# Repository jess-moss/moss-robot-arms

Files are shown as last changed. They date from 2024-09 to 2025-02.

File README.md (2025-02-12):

> [!IMPORTANT]
> For use with [LeRobot](https://github.com/huggingface/lerobot)  we now recommend building or purchasing the [SO100](https://github.com/TheRobotStudio/SO-ARM100) arm instead. While the Moss v1 robot is still supported, it will be deprecated. Additionally, 3D-printed parts for the SO100 are now available for purchase if you don't have a printer. If you already have a Moss v1, you could disassemble it and create a SO100 using the same motors. 
>
> For instructions on building and setting up the SO100, follow this [tutorial](https://github.com/huggingface/lerobot/blob/main/examples/10_use_so100.md).

# moss-robot-arms
moss-robot-arms Beta version 1.0.

A repository for affordable, easy-to-assemble robot arms designed for teleoperation applications. 

## Assembly Instructions

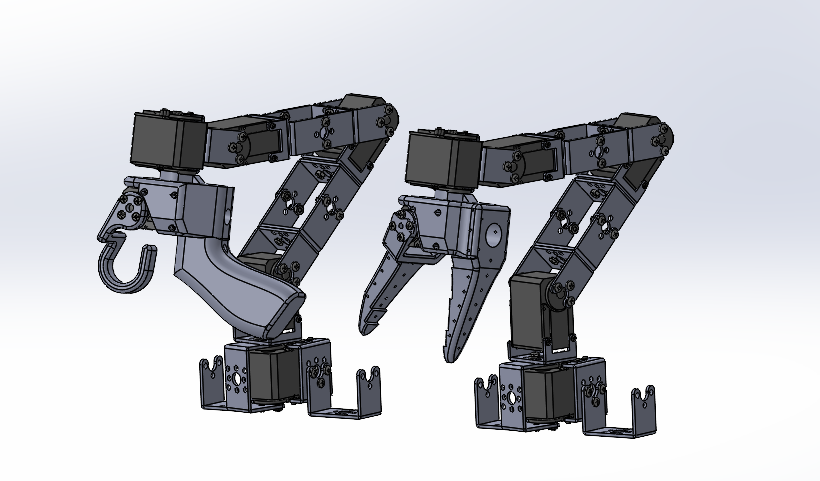
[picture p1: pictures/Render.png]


## Sourcing Parts
Note: The follower and leader arm for this teleoperation setup will have the same off the shelf parts. If you plan on creating the classic teleoperation set up to be used with the `LeRobot` library please buy from the Parts for 2 arms below. Note prices and items may vary slightly depending on geographic location.

/!\ Warning: We only have links for US, EU and CN for now. If you find links for other countries, please create an issue or PR so that we add them to the list.

### Parts For Two Arms (Standard Teleoperation Setup):
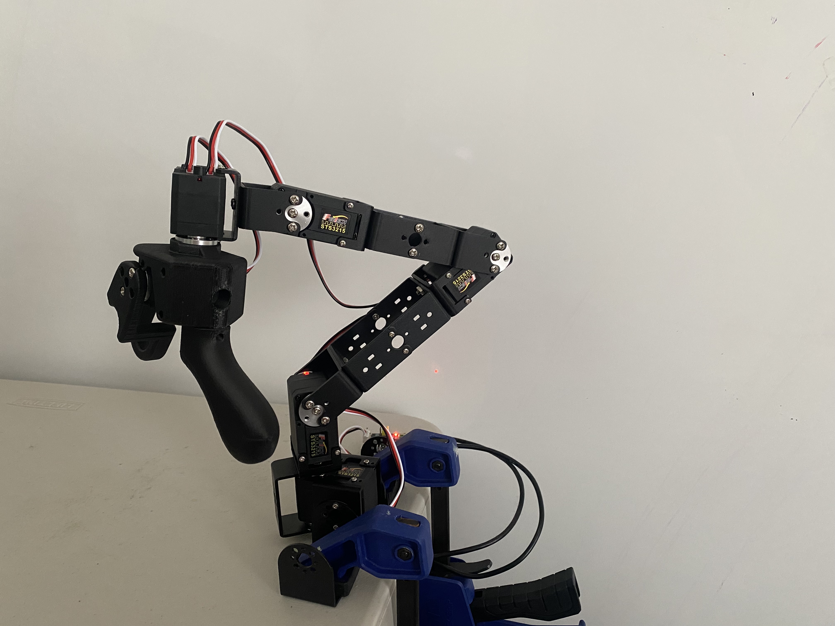
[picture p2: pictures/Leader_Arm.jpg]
Leader Arm
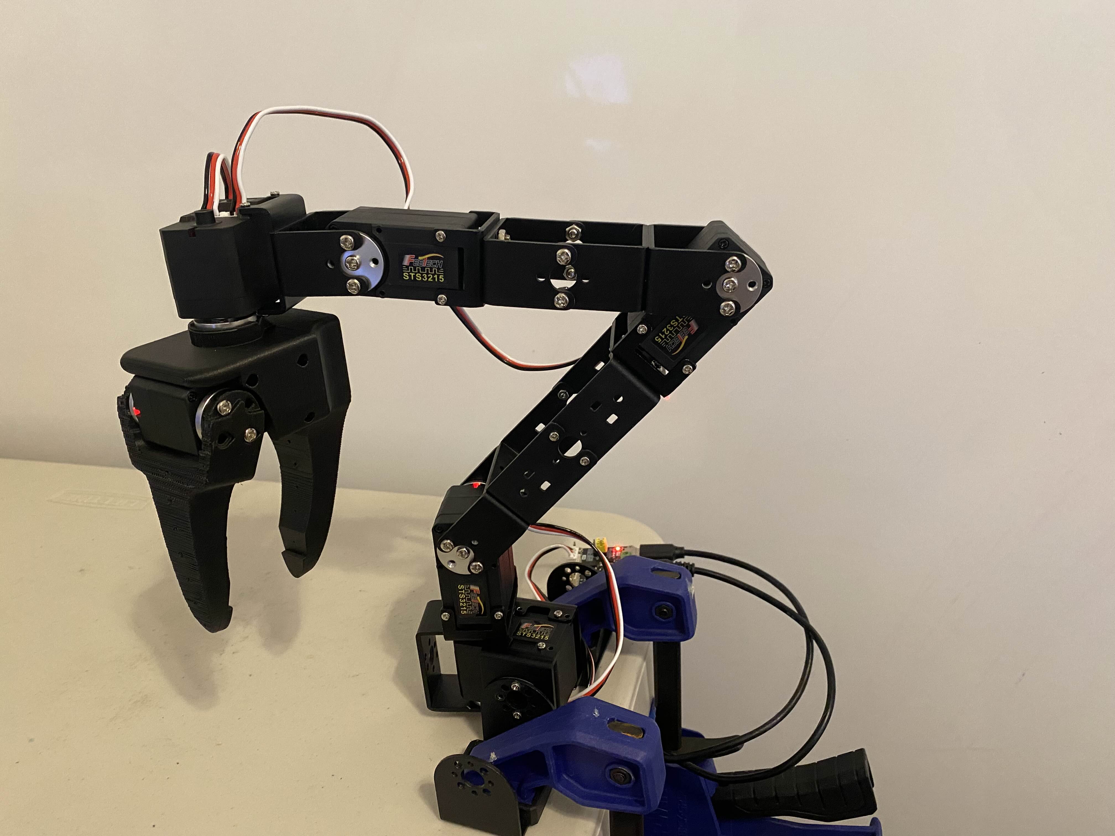
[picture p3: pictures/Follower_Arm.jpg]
Follower Arm
 

| Part | Amount | Unit Cost (US) | Buy US | Unit Cost (EU) | Buy EU | Unit Cost (RMB) | Buy CN |
|---|---|---|---|---|---|---|---|
| STS3215 Servo<sup>[1](#myfootnote1)</sup> | 12 | $14 | [Alibaba](https://www.alibaba.com/product-detail/Top-Seller-Low-Cost-Feetech-STS3215_1600999461525.html) | 13€ | [Alibaba](https://www.alibaba.com/product-detail/Top-Seller-Low-Cost-Feetech-STS3215_1600999461525.html) | ￥97.72 | [TaoBao](https://item.taobao.com/item.htm?id=712179366565&skuId=5268252241438) |
| Motor Control Board | 2 | $5 | [Waveshare](https://www.waveshare.com/bus-servo-adapter-a.htm) - [Amazon](https://www.amazon.com/Control-Circuit-Suitable-Supports-Controlling/dp/B0CKT8BN73/ref=asc_df_B0CKT8BN73/) | 4€ | [Waveshare](https://www.waveshare.com/bus-servo-adapter-a.htm)-[Amazon](https://www.amazon.fr/-/en/dp/B0CJ6RYC9J/ref=sr_1_3)| ￥27 | [TaoBao](https://detail.tmall.com/item.htm?id=738817173460&skuId=5096283384143) |
| Bracket Set | 20 | $3 | [Alibaba](https://www.alibaba.com/product-detail/STS3215-Metal-brackets-for-FEETECH-7_1600836829515.html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) | 2€ | [Alibaba](https://www.alibaba.com/product-detail/STS3215-Metal-brackets-for-FEETECH-7_1600836829515.html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) | --- | --- |
| U Bracket | 20 | --- | --- | --- | --- | ￥6 | [TaoBao](https://item.taobao.com/item.htm?id=615340872015&skuId=4472922777845) |
| Bottom Bracket | 6 | --- | --- | --- | --- | ￥6 | [TaoBao](https://item.taobao.com/item.htm?id=615340872015&skuId=4472922777847) |
| Side Bracket | 6 | --- | --- | --- | --- | ￥6 | [TaoBao](https://item.taobao.com/item.htm?id=615340872015&skuId=4472922777846) |
| USB-C Cable 2 pcs | 1 | $7 | [Amazon](https://www.amazon.com/Charging-etguuds-Charger-Braided-Compatible/dp/B0B8NWLLW2/?th=1) | 7€ | [Amazon](https://www.amazon.fr/dp/B07BNF842T) | ￥23.9*2 | [TaoBao](https://detail.tmall.com/item.htm?id=44425281296&skuId=5611379016222) |
| Power Supply<sup>[2](#myfootnote2)</sup> | 2 | $10 | [Amazon](https://www.amazon.com/Facmogu-Switching-Transformer-Compatible-5-5x2-1mm/dp/B087LY41PV/) | 13€ | [Amazon](https://www.amazon.fr/-/en/dp/B01HRR9GY4/) | ￥22.31 | [TaoBao](https://item.taobao.com/item.htm?id=544824248494&skuId=4974994129990) |
| Table Clamp 4pcs | 1 | $9 | [Amazon](https://www.amazon.com/dp/B0CY899V9V) | 8€ | [Amazon](https://www.amazon.fr/-/en/dp/B08HZ1QRBF/)| ￥7.8 | [TaoBao](https://detail.tmall.com/item.htm?id=738636473238&skuId=5505939904942) |
| Lowstrength Threadlocker<sup>[3](#myfootnote3)</sup> | 1 | $9 | [Amazon](https://www.amazon.com/Loctite-Threadlocker-Automotive-High-Temperature-Non-Corrosive/dp/B0002KKTT0/)| 11€ | [Amazon](https://www.amazon.fr/-/en/dp/B000HBGHFY/) | ￥81 | [TaoBao](https://detail.tmall.com/item.htm?id=652665229827&skuId=5125512809535) |
| Screwdriver Set (includes Phillips #000, #00, #0, #1) | 1 | $6 | [Amazon](https://www.amazon.com/Precision-Phillips-Screwdriver-Electronics-Computer/dp/B0DB227RTH) | 10€ | [Amazon](https://www.amazon.fr/dp/B08ZXVMVYD/) | ￥14.9 | [TaoBao](https://detail.tmall.com/item.htm?id=675684600845&skuId=4856851392176) |
| Wrench<sup>[4](#myfootnote5)</sup> | 1 | $5 | [Amazon](https://www.amazon.com/uxcell-Metric-Double-Wrench-5-5mm/dp/B07D4B8GWW/) | 4€ | [Amazon](https://www.amazon.fr/-/en/dp/B075DML8KB/) | ￥8.9 | [TaoBao](https://detail.tmall.com/item.htm?id=735857252241&skuId=5685349146062) |
| Total |---| $288 |---| 274€ |---|￥1631.46|---|

### Parts for One Arm:

| Part | Amount | Unit Cost (US) | Buy US | Unit Cost (EU) | Buy EU | Unit Cost (RMB) | Buy CN |
|---|---|---|---|---|---|---|---|
| STS3215 Servo<sup>[1](#myfootnote1)</sup> | 6 | $14 | [Alibaba](https://www.alibaba.com/product-detail/Top-Seller-Low-Cost-Feetech-STS3215_1600999461525.html) | 13€ | [Alibaba](https://www.alibaba.com/product-detail/Top-Seller-Low-Cost-Feetech-STS3215_1600999461525.html) | ￥97.72 | [TaoBao](https://item.taobao.com/item.htm?id=712179366565&skuId=5268252241438) |
| Motor Control Board | 1 | $5 | [Waveshare](https://www.waveshare.com/bus-servo-adapter-a.htm) - [Amazon](https://www.amazon.com/Control-Circuit-Suitable-Supports-Controlling/dp/B0CKT8BN73/ref=asc_df_B0CKT8BN73/) | 4€ | [Waveshare](https://www.waveshare.com/bus-servo-adapter-a.htm)-[Amazon](https://www.amazon.fr/-/en/dp/B0CJ6RYC9J/ref=sr_1_3)| ￥27 | [TaoBao](https://detail.tmall.com/item.htm?id=738817173460&skuId=5096283384143) |
| Bracket Set | 10 | $3 | [Alibaba](https://www.alibaba.com/product-detail/STS3215-Metal-brackets-for-FEETECH-7_1600836829515.html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) | 2€ | [Alibaba](https://www.alibaba.com/product-detail/STS3215-Metal-brackets-for-FEETECH-7_1600836829515.html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) | --- | --- |
| U Bracket | 10 | --- | --- | --- | --- | ￥6 | [TaoBao](https://item.taobao.com/item.htm?id=615340872015&skuId=4472922777845) |
| Bottom Bracket | 3 | --- | --- | --- | --- | ￥6 | [TaoBao](https://item.taobao.com/item.htm?id=615340872015&skuId=4472922777847) |
| Side Bracket | 3 | --- | --- | --- | --- | ￥6 | [TaoBao](https://item.taobao.com/item.htm?id=615340872015&skuId=4472922777846) |
| USB-C Cable 2 pcs | 1 | $7 | [Amazon](https://www.amazon.com/Charging-etguuds-Charger-Braided-Compatible/dp/B0B8NWLLW2/?th=1) | 7€ | [Amazon](https://[www.amazon.com/Charging-etguuds-Charger-Braided-Compatible/dp/B0B8NWLLW2/?th=1](https://www.amazon.fr/dp/B07BNF842T/)) | ￥23.9 | [TaoBao](https://detail.tmall.com/item.htm?id=44425281296&skuId=5611379016222) |
| Power Supply<sup>[2](#myfootnote2)</sup> | 1 | $10 | [Amazon](https://www.amazon.com/Facmogu-Switching-Transformer-Compatible-5-5x2-1mm/dp/B087LY41PV/) | 13€ | [Amazon](https://www.amazon.fr/-/en/dp/B01HRR9GY4/) | ￥22.31 | [TaoBao](https://item.taobao.com/item.htm?id=544824248494&skuId=4974994129990) |
| Table Clamp 2pcs | 1 | $5 | [Amazon](https://www.amazon.com/Clamp-Hanger-Storage-Clamps-Mount/dp/B0C1GYSVCS?rps=1&sr=1-2) | 8€ | [Amazon](https://www.amazon.fr/-/en/dp/B08HZ1QRBF/)| ￥7.8 | [TaoBao](https://detail.tmall.com/item.htm?id=738636473238&skuId=5505939904942) |
| Lowstrength Threadlocker<sup>[3](#myfootnote3)</sup> | 1 | $9 | [Amazon](https://www.amazon.com/Loctite-Threadlocker-Automotive-High-Temperature-Non-Corrosive/dp/B0002KKTT0/)| 11€ | [Amazon](https://www.amazon.fr/-/en/dp/B000HBGHFY/) | ￥81 | [TaoBao](https://detail.tmall.com/item.htm?id=652665229827&skuId=5125512809535) |
| Screwdriver Set (includes Phillips #000, #00, #0, #1) | 1 | $6 | [Amazon](https://www.amazon.com/Precision-Phillips-Screwdriver-Electronics-Computer/dp/B0DB227RTH) | 10€ | [Amazon](https://www.amazon.fr/dp/B08ZXVMVYD/) | ￥14.9 | [TaoBao](https://detail.tmall.com/item.htm?id=675684600845&skuId=4856851392176) |
| Wrench<sup>[4](#myfootnote4)</sup> | 1 | $5 | [Amazon](https://www.amazon.com/uxcell-Metric-Double-Wrench-5-5mm/dp/B07D4B8GWW/) | 4€ | [Amazon](https://www.amazon.fr/-/en/dp/B075DML8KB/) | ￥8.9 | [TaoBao](https://detail.tmall.com/item.htm?id=735857252241&skuId=5685349146062) |
| Total |---| $159 |---| 153€ |---|868.13|---|

## Printing the Parts
A variety of 3D printers are acceptable to print the parts necessary of the follower and leader arm. Follow the steps below to ensure a good print.

1. Choose a printer: The STL files provided ready to print on many FDM printers. Below are the tested and suggested settings though others may work.
   1. Material: PLA
   2. Nozzle Diameter and Precision: 0.4mm nozzle diameter at 0.2mm layer height or 0.6mm nozzle at 0.4mm layer height.
   3. Infill Density: 13%
   4. Sample Printers: [Prusa Mini+](https://www.prusa3d.com/product/original-prusa-mini-semi-assembled-3d-printer-4/), [UP Plus 2](https://shop.tiertime.com/product/tiertime-up-plus-2-3d-printer/), [Ender3](https://www.amazon.com/Comgrow-Creality-Ender-Aluminum-220x220x250mm/dp/B07BR3F9N6/).
2. Set up the printer
   1. Setup and Takedown
      1. Ensure that the printer is calibrated and the bed level is correctly set using the printer specific instructions.
      2. Clean the print bed, making sure it is free from dust, or grease. If cleaning the bed using water, or other liquid, dry the bed.
      3. If your printer recommends it, use a standard glue stick and apply a thin, even layer of glue across the print area of the bed. Avoid clumping or uneven application.
      4. Load the printer filament using printer specific instructions.
      5. Ensure the printer settings match the ones suggested above (most printers have multiple settings so choose the ones that most closely match).
      6. Set for supports everywhere but ignore slopes greater than 45 degrees to the horizontal.
      7. There should be no supports in the screw holes with horizontal axes.
3. Print the two files found in `so_100_gripper_parts`, which are listed below.
   1. `Print_Follower_SO_ARM100_08k_Gripper.STL`
   2. `Print_Leader_SO_ARM100_08k_Gripper.STL`
4. Take Down
   1. After the print is done, use the putty knife to scrape the parts off the print bed.
   2. Remove any support material from parts.
   3. Reapply the glue stick before starting the next print.

## Assembling the Parts
Construct the leader and follower arms using the [Assembly Video](https://www.youtube.com/watch?v=DA91NJOtMic). After you assemble the two arms from the video, power the leader and follower arm using the 5V power supplies. In addition, plug each arm into your computer using a USB-C cable.

## Configure
While this robot can be programmed in a variety of manners, it is suggested to use with [LeRobot](https://github.com/huggingface/lerobot/blob/main/examples/7_get_started_with_real_robot.md).

Join the project for support and development on the [discord server](https://discord.gg/ggrqhPTsMe).

## Footnotes
<a name="myfootnote1">1</a>: The STS3215 arm comes in two sizes. The 7.4V has a stall torque of 16.5kg.cm at 6V (and likely slightly less for a 5V power supply). The 12V version has a stall torque of 30kg.cm. While we found the 7.4V to be sufficient, if you would like more powerful motors you can buy the 12V version [here](https://www.alibaba.com/product-detail/12V-30KG-STS3215-High-Torque-Intelligent_1600990786556.html). Note if you do this, you will also have to buy a 12V 5A+ power supply instead of a 5V one above, but all other components will remain the same.\
<a name="myfootnote2">2</a>: IMPORTANT: If you buy the 12V STS3215 motors, you should buy the [12V 5A+ power supply](https://www.amazon.com/Converter-100-220V-Transformer-5-5x2-1mm-Accessories/dp/B08C594VNP/) instead of the 5V power supply provided. \
<a name="myfootnote3">3</a>: While Loctite is not strictly necessary, it does help to ensure screws do not loosen overtime, and is recommended whenever you have a the M3 screw fastening into the M3 nut. You only need a small dot of it. \
<a name="myfootnote4">4</a>: You can either use a 5.5mm or 7/32" wrench, as they are both compatible with the M3 nuts. In a pinch you can also use needle-nose or other pliers but a wrench does help with assembly.

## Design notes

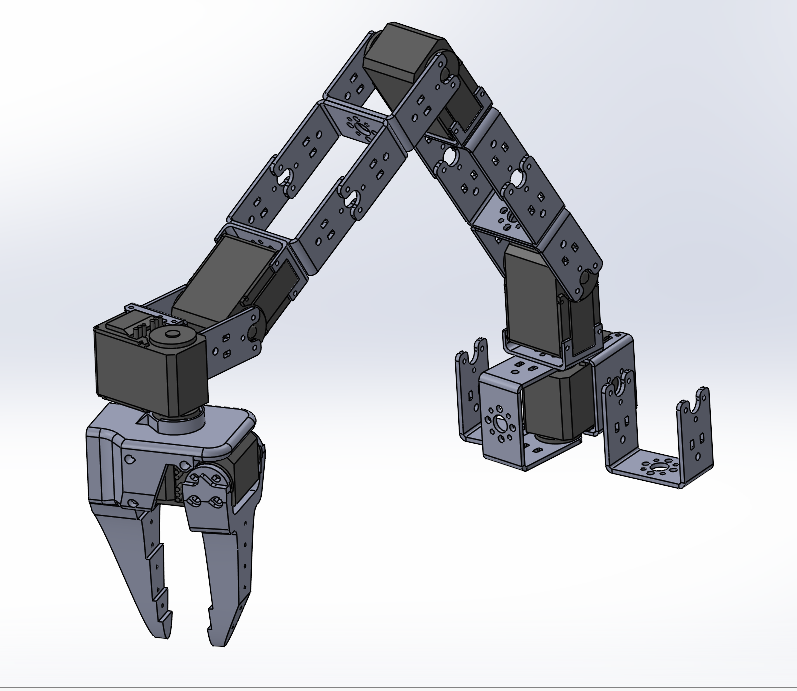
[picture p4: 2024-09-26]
pictures/Follower_Render.png

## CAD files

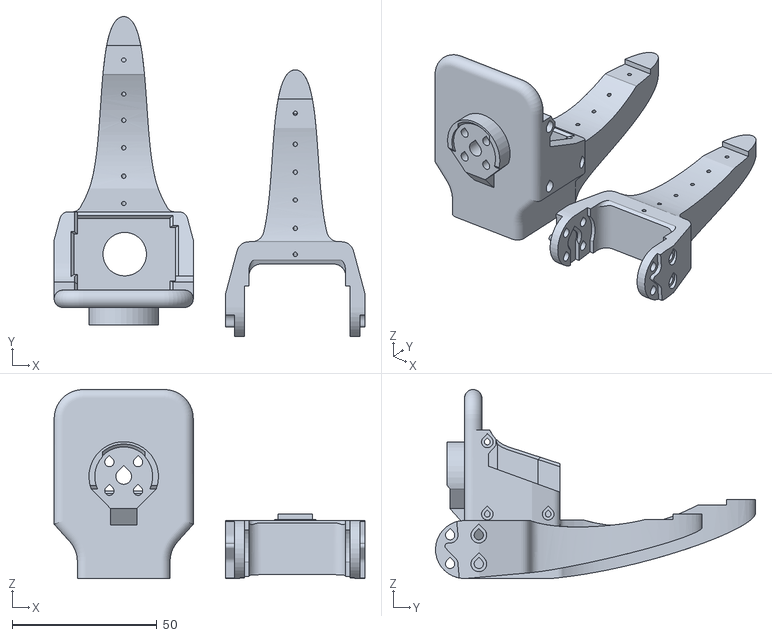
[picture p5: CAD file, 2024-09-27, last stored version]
so_100_gripper_parts/follower_gripper/SO_100_Follower_Gripper.STL
107.2 x 110.4 x 65.2

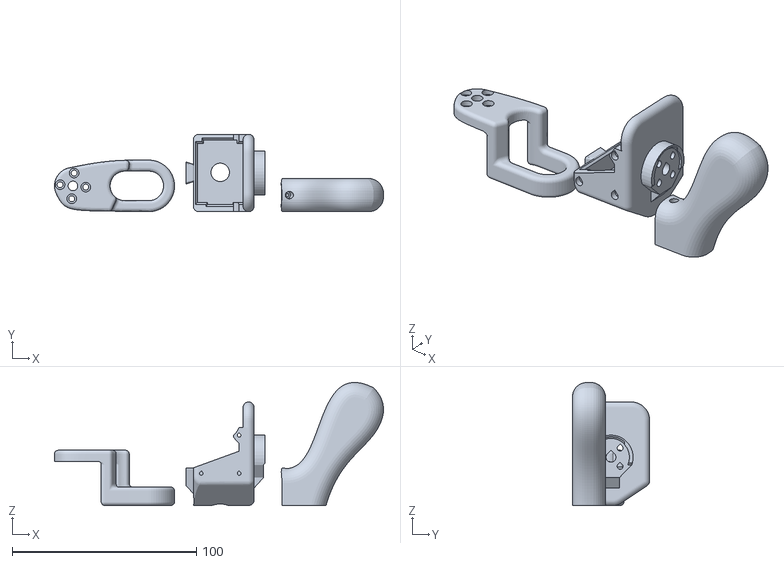
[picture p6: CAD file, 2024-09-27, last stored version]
so_100_gripper_parts/leader_gripper/SO_100_Leader_Gripper.STL
178.5 x 42.0 x 66.8

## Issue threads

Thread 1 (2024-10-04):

Bracket not available on Alibaba anymore

Positron00, 2024-10-04:
Hi,

The Bracket Set in the parts list links to an Alibaba page that says it's no longer available. Do you have an alternative source for them? Thanks!

Bracket Set	18	$3	[Alibaba](https://www.alibaba.com/product-detail/STS3215-Metal-brackets-for-FEETECH-7_1600836829515.html)

jess-moss, 2024-10-04:
Hello! Yes, unfortunately, this week is a Chinese national holiday, so the Feetech team is out of office, but as soon as they are back next week, I will provide an alternate link. Apologies for the delay.

jess-moss, 2024-10-29:
Hello They are available again. Sorry about any confusion!

Closed 2024-10-29.

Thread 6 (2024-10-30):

Should M3x4 screws be purchased separately?

RonanKMcGovern, 2024-10-30:
I remember at the hackathon that they were in a separate box, which is making me wonder if they come with the brackets or motors? Thanks

jess-moss, 2024-11-04:
Hello, they should come with the brackets! We didn't have this link sorted out yet for the hackathon unfortunately but it should be now! Let me know if you run into any issues!

Closed 2024-11-04.

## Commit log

2024-09-19 Added liscense and BoM
2024-09-21 changed and condensed BoM
2024-09-24 updated servos to 7.4V and prackets to QTY 9
2024-09-26 updated BoM
2024-09-27 Added STL and new picture.
    [SO_100_Follower_Gripper.STL, SO_100_Leader_Gripper.STL]
2024-09-30 Added pictures, and updated BoM.
    [SO_100_Follower_Gripper.STL, SO_100_Leader_Gripper.STL]
2024-09-30 Updated power suppply.
2024-10-01 Updated STL files to latest version from SO100 Arm repo.
    [SO_100_Follower_Gripper.STL, SO_100_Leader_Gripper.STL]
2024-10-02 Updated motor link.
2024-10-04 Added 12V STS3215 as an option.
2024-10-16 Updated bracket list and removed washers (no longer needed).
2024-10-22 Added new leader gripper.
2024-10-29 Fixed number in bracket set.
2024-10-29 Commited assembly video.
2024-10-29 Updated motors.
2025-02-09 Update clamps to have >4 pcs
